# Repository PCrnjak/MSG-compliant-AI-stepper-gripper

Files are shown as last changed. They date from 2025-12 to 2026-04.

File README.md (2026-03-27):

> [!CAUTION]
> The gripper is still in BETA release meaning it will have some bugs from hardware to software!
>

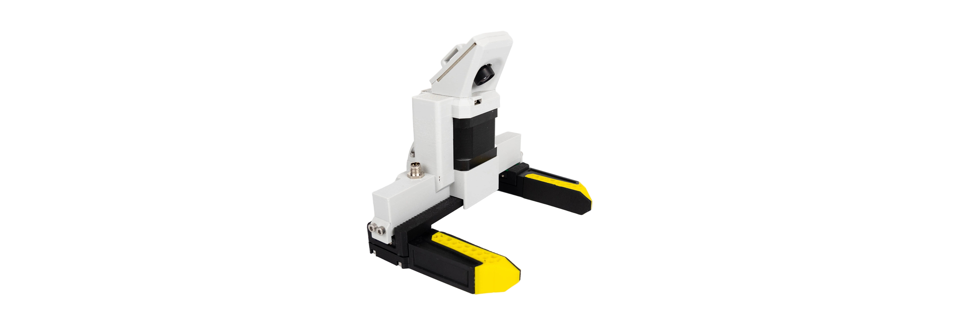
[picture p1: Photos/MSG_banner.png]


<div align="center">

# MSG-compliant-AI-stepper-gripper


     
<p align="center">
  
  
  
  
  
  
</p>

## [▶️YouTube🔴 Video of Gripper in Action!](https://youtu.be/YUvNXfaHM6s)

</div>

## 📖 Project Overview
The **MSG compliant AI stepper gripper** is built around [StepFOC stepper drivers](https://source-robotics.com/products/stepfoc-stepper-controller), which enable precise FOC-based force control on standard stepper motors. This makes it well-suited for assembly tasks, human-robot collaboration, and AI data collection applications — including embodied AI, teleoperation, and VLA training — thanks to its camera-friendly design.

**The gripper is modular in two key ways:**

| Option | Variants | Notes |
|---|---|---|
| Rail length | 100 mm, 150 mm, 200 mm | Determines maximum grip span |
| Stepper length | 21.5 mm, 40 mm, 60 mm | Determines maximum grip force output |

**All mechanical files, firmware, and software are open source, allowing you to attach a custom gripping tool and integrate the gripper with any robotic arm or platform.**

## ⚒️How to build / Where to buy?

You can buy MSG gripper on our website: https://source-robotics.com/products/msg-gripper

If you want to Source all the parts yourself and build your own follow these steps:

Print files from the STEP files folder based on your chosen configuration:

| Rail Size | Folders to Print |
|---|---|
| 100 mm | [Common parts](STEP%20files/Common%20parts) + [Linear rail dependant parts/100mm rail](STEP%20files/Linear%20rail%20dependant%20parts/100mm%20rail) + [Stepper dependant parts/\<your stepper size\>](STEP%20files/Stepper%20dependant%20parts) |
| 150 mm | [Common parts](STEP%20files/Common%20parts) + [Linear rail dependant parts/150mm rail](STEP%20files/Linear%20rail%20dependant%20parts/150mm%20rail) + [Stepper dependant parts/\<your stepper size\>](STEP%20files/Stepper%20dependant%20parts) |
| 200 mm | [Common parts](STEP%20files/Common%20parts) + [Linear rail dependant parts/200mm rail](STEP%20files/Linear%20rail%20dependant%20parts/200mm%20rail) + [Stepper dependant parts/\<your stepper size\>](STEP%20files/Stepper%20dependant%20parts) |

* Source all the parts from the [BOM](https://github.com/PCrnjak/MSG-compliant-AI-stepper-gripper/blob/main/BOM.md)
* Follow [Assembly instructions ](https://youtu.be/EosuDy-heqM) or [Video instructions](https://youtu.be/EosuDy-heqM) to assemble your gripper
* Follow [DOCS](https://source-robotics.github.io/MSG-gripper-docs/) to get your gripper up and running.

## 📚Documentation:

| Resource | Description |
|---|---|
| [Official website](https://source-robotics.com) | Buy the MSG gripper or explore other Source Robotics products |
| [DOCS](https://source-robotics.github.io/MSG-gripper-docs/) | Getting started, wiring, configuration, and full API reference |
| [Python API](https://github.com/PCrnjak/Spectral-BLDC-Python/tree/main) | Control the gripper from Python over CAN bus |
| [BOM](https://github.com/PCrnjak/MSG-compliant-AI-stepper-gripper/blob/main/BOM.md) | Complete list of parts needed to build the gripper |
| [Building instructions *(coming soon)*](https://github.com/PCrnjak/MSG-compliant-AI-stepper-gripper/tree/main/Building%20instructions) | Mechanical assembly walkthrough |
| [URDF & MJCF files](/MSG_gripper_description/) | Ready-to-use robot description files for ROS2, Gazebo, and MuJoCo |
| [ROS2 package — MSG gripper](https://github.com/BiomechatronicsLab/source_robotics_msg_gripper_ros2) | ROS2 driver and example nodes for the MSG gripper |
| [ROS2 package — SSG48 gripper](https://github.com/Lass6230/ssg48_adaptive_electric_gripper_ros2) | ROS2 driver and example nodes for the SSG48 gripper (Should work with MSG also) |

## 💻Quick start code example

```python
import Spectral_BLDC as Spectral
import time

Communication1 = Spectral.CanCommunication(bustype='slcan', channel='COM20', bitrate=1000000)
Motor1 = Spectral.SpectralCAN(node_id=0, communication=Communication1)

Motor1.Send_Clear_Error()
Motor1.Send_gripper_calibrate()
time.sleep(4)

temp_var = 0
while True:
   if temp_var == 0:
      Motor1.Send_gripper_data_pack(50,100,700,1,1,0,0) 
      temp_var = 1
   elif temp_var == 1:
      Motor1.Send_gripper_data_pack(240,100,700,1,1,0,0) 
      temp_var = 0

   message, UnpackedMessageID = Communication1.receive_can_messages(timeout=0.2) 

   if message is not None:
      print(f"Message is: {message}")
      print(f"Node ID is : {UnpackedMessageID.node_id}")
      print(f"Message ID is: {UnpackedMessageID.command_id}")
      print(f"Error bit is: {UnpackedMessageID.error_bit}")
      print(f"Timestamp is: {message.timestamp}")

   time.sleep(3)
```

## 🌐 More about MSG gripper

| YouTube | Instagram | Twitter | LinkedIn |
|---|---|---|---|
|  |  |  |  |

| Discord | Forum | Hackaday | Blog |
|---|---|---| ---|
|  |  |  |  

## ⚠️ Safety, Liability & Disclaimer
This project includes experimental software, hardware designs, and assembly documentation that are still under development and may contain bugs, errors, or incomplete features. By using, building, or modifying this project, you acknowledge that:

* You use this project entirely at your own risk
* You are solely responsible for safe assembly, testing, and operation
* No guarantee is made regarding correctness, safety, or reliability
* The authors are not responsible for any damage, injury, or loss resulting from the use or misuse of this project
* Hardware performance and safety depend on user assembly, component quality, calibration, and handling, which cannot be guaranteed
* This project is provided “as is.” If you choose to build a device yourself using these files, designs, or instructions, you do so without any warranties or guarantees, including regarding safety, reliability, or suitability for any particular purpose.

THIS PROJECT INVOLVES LETHAL VOLTAGES AND OTHER SERIOUS HAZARDS THAT CAN CAUSE SEVERE INJURY. YOU MUST READ THE FULL [SAFETY WARNING AND DISCLAIMER DOCUMENT](SAFETY_WARNING_AND_DISCLAIMER.md)  BEFORE USING ANY PROJECT FILES. BY PROCEEDING, YOU ACKNOWLEDGE AND ACCEPT ALL RISKS AND AGREE TO USE THIS PROJECT ENTIRELY AT YOUR OWN RESPONSIBILITY.

## 💸Support us

The majority of this project is open source and freely available to everyone. Your assistance, whether through donations or advice, is highly valued. Thank you!

 


## 🛡️ Licensing
 Project is under [CERN Open Hardware Licence Version 2 - Strongly Reciprocal](https://github.com/PCrnjak/MSG-compliant-AI-stepper-gripper?tab=CERN-OHL-S-2.0-1-ov-file)

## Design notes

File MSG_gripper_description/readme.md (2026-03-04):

# Source Robotics MSG gripper Description (MJCF) & URDF

> [!IMPORTANT]
> Requires MuJoCo 3.1.3 or later.

## Changelog

See [CHANGELOG.md](./CHANGELOG.md) for a full history of changes.

## Overview

This package contains a simplified robot description (MJCF) and URDF files of the [MSG gripper](https://source-robotics.com/products/msg-gripper) developed by [Source Robotics](https://source-robotics.com/).

There are 2 available MJCF files.

## Online mujoco viewer

https://mujoco-viewer.org/

## URDF folder

[URDF](./URDF/) folder contains:
* MSG gripper

More about URDF here: [Link](./urdf.md)

## URDF → MJCF derivation steps

1. Loaded the URDF into MuJoCo and saved a corresponding MJCF.
2. Manually edited the MJCF to extract common properties into the `<default>` section.
3. Added position-controlled actuators for the arm.
4. Added `scene.xml` which includes the robot, with a textured groundplane, skybox, and haze.

## License

This model is released under an [Apache-2.0 License](LICENSE).

## References

Mjcf reference Mujoco managerie
- references: 
- https://mujoco.readthedocs.io/en/stable/XMLreference.html
- https://github.com/google-deepmind/mujoco_menagerie/tree/main/ufactory_lite6
- https://github.com/google-deepmind/mujoco_menagerie/blob/main/trossen_vx300s/vx300s.xml 
- https://github.com/google-deepmind/mujoco_menagerie/blob/main/aloha/aloha.xml
- https://github.com/google-deepmind/mujoco_menagerie/blob/main/franka_emika_panda/panda.xml 
- https://github.com/jeongeun980906/lerobot-mujoco-tutorial/blob/master/asset/robotis_omy/omy.xml

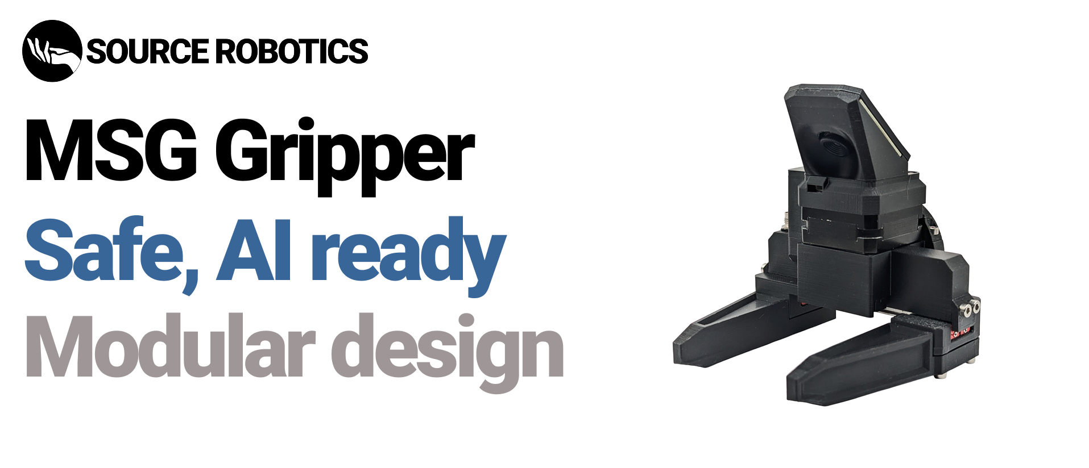
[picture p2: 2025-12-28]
Photos/MSG gripper.png

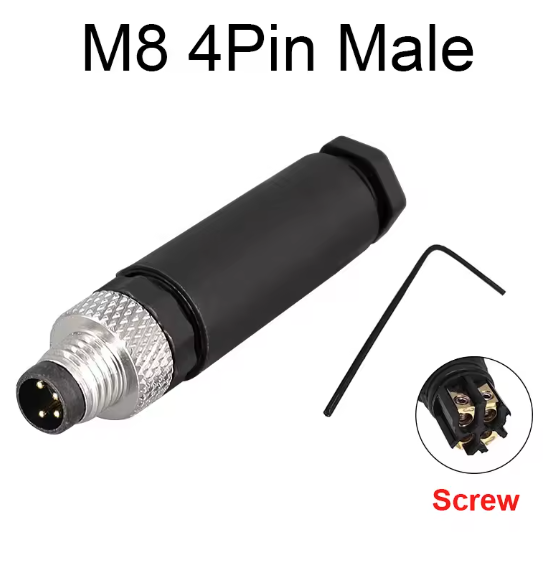
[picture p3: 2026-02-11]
Photos/M8 male.png

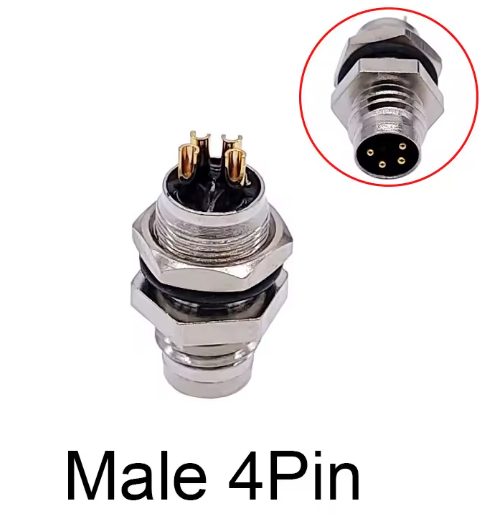
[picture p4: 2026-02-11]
Photos/M8connectormale4pin.png

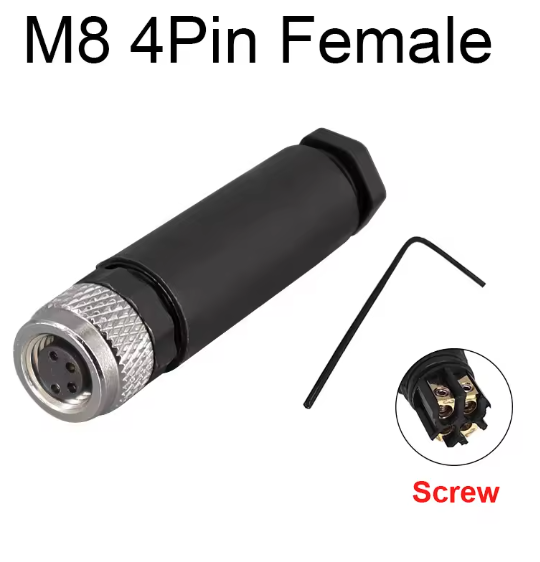
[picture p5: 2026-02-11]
Photos/M8_female.png

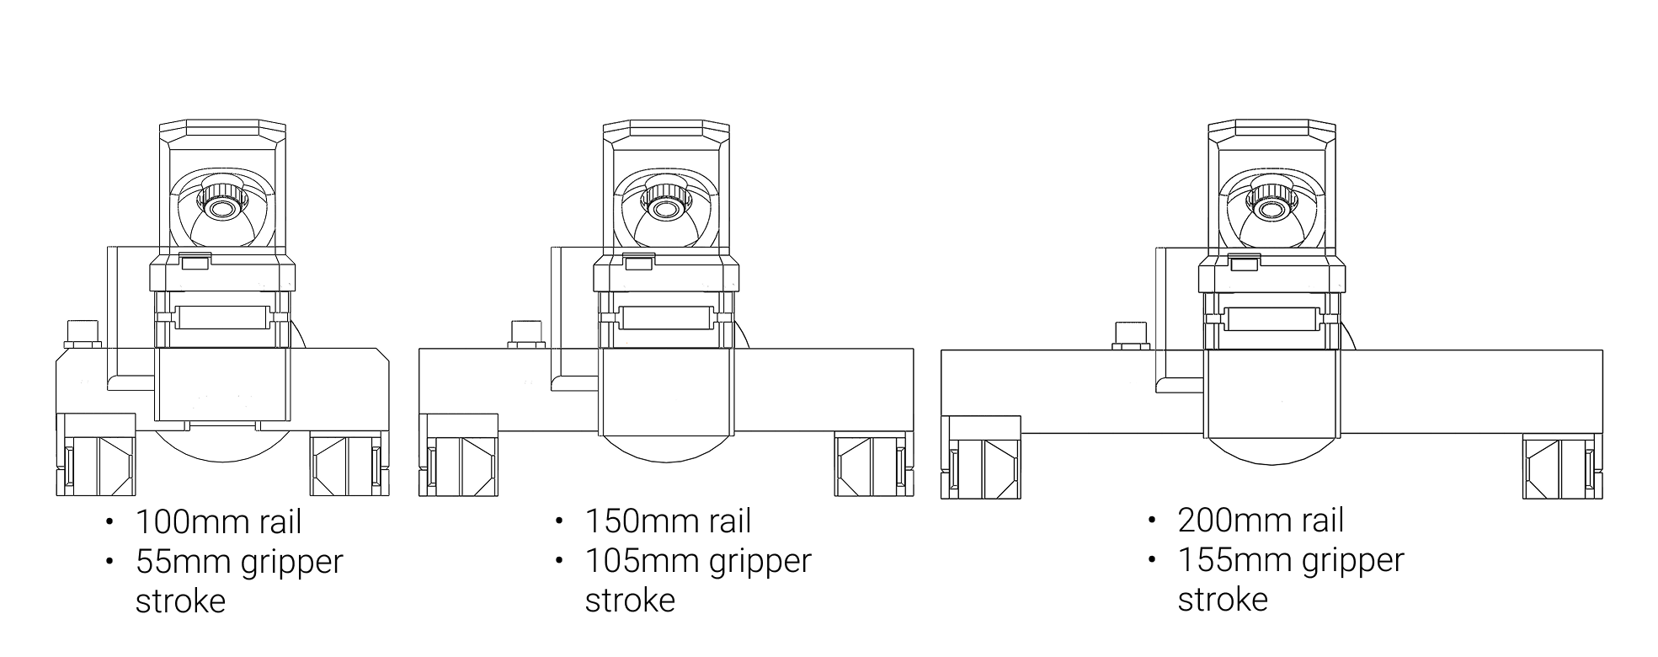
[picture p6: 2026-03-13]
Photos/Gripper_strokes.png

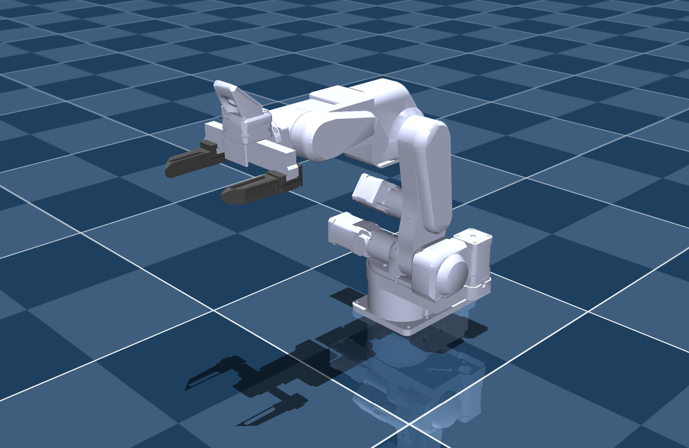
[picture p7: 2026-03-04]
MSG_gripper_description/PAR6_MSG_image.png

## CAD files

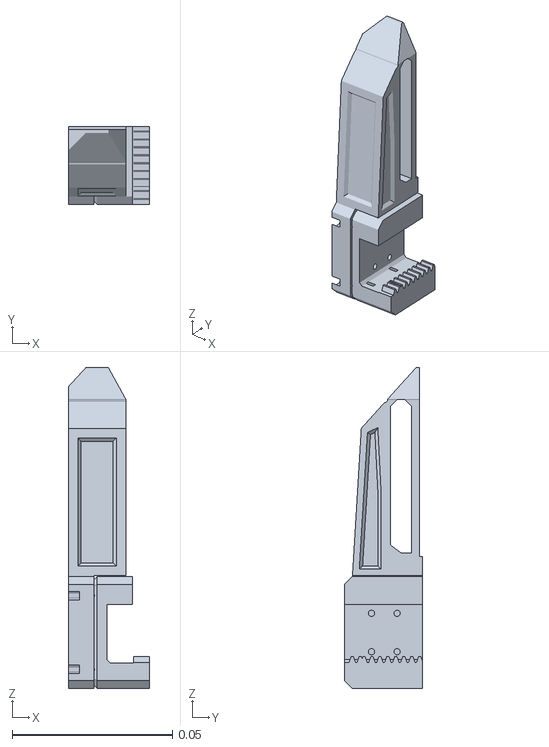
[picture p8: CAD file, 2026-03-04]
MSG_gripper_description/assets/jaw1_MSG.STL
0.0254 x 0.0244 x 0.1

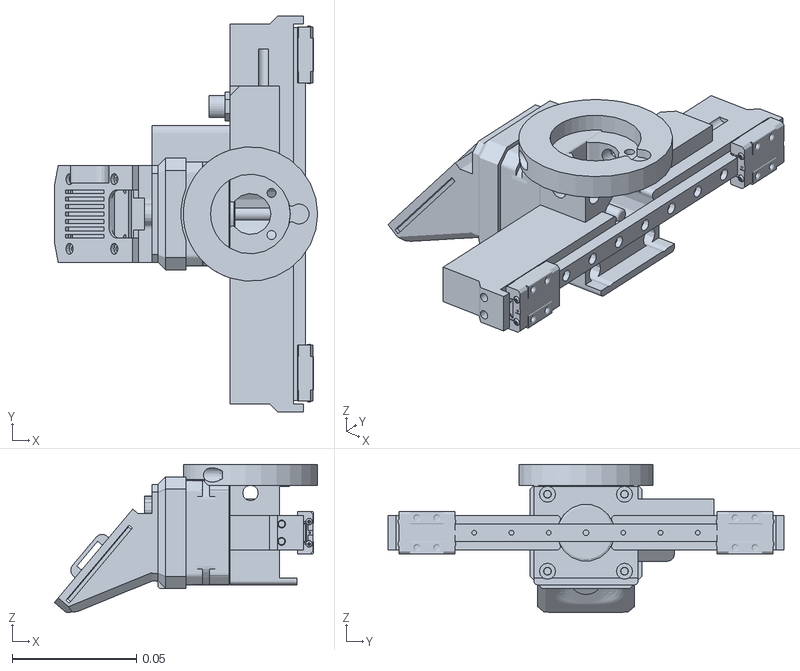
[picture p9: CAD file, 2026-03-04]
MSG_gripper_description/URDF/msg_gripper/meshes/gripper.STL
0.106 x 0.159 x 0.0597

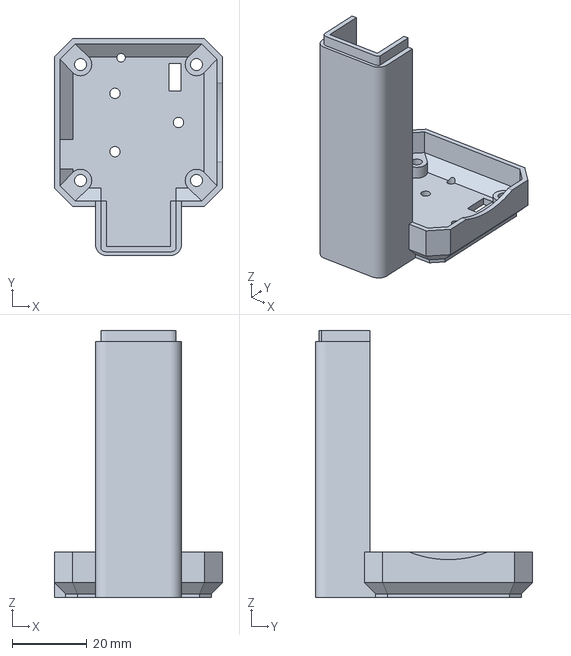
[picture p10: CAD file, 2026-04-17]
Print files/Stepper_cover_60mm.3mf
45.0 x 58.1 x 71.4 mm

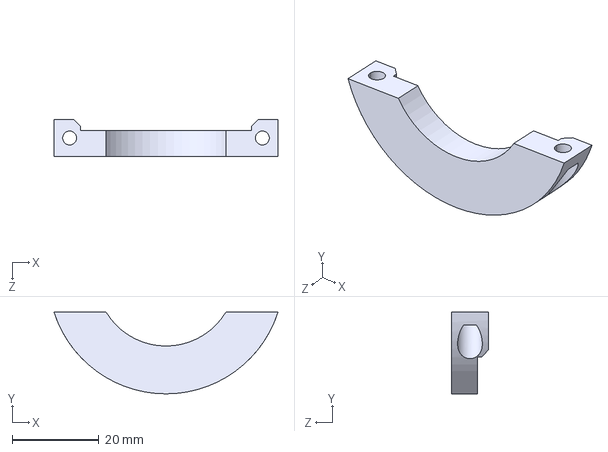
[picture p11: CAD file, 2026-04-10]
STEP files/Common parts/ring_cover.STEP
51.5 x 18.8 x 8.50 mm

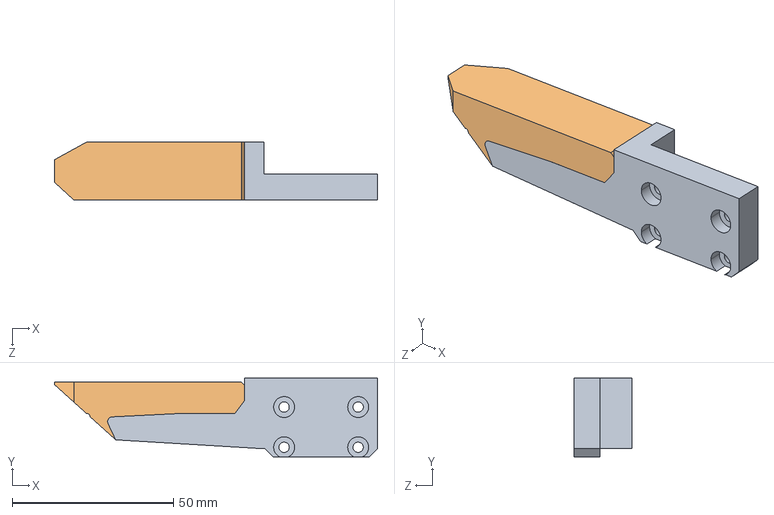
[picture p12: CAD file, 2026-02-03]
STEP files/Gripper jaws attachment/MSG_JAW_TPU_GLUE.STEP
100.3 x 24.4 x 18.0 mm

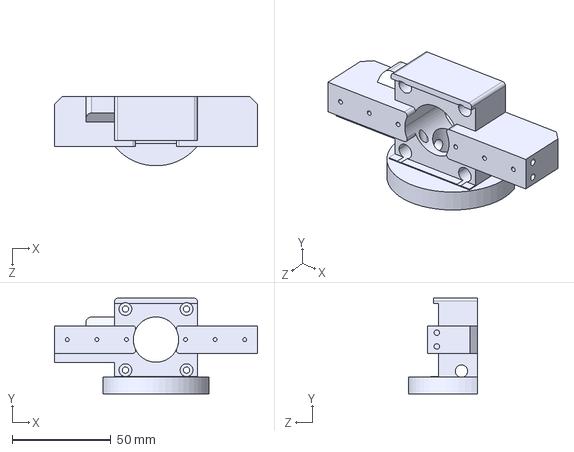
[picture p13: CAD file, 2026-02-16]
STEP files/Linear rail dependant parts/100mm rail/MSG_Gripper_body_100mm.STEP
103.0 x 48.5 x 35.3 mm

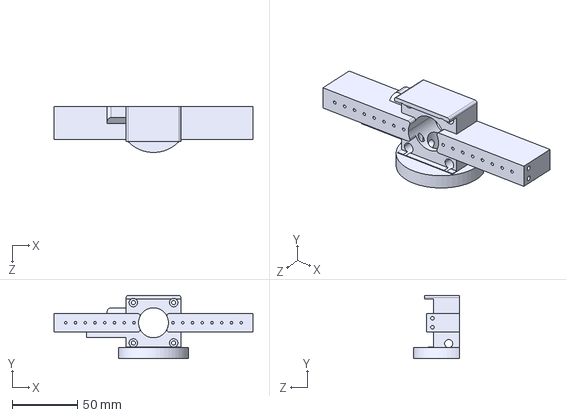
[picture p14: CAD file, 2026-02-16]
STEP files/Linear rail dependant parts/150mm rail/MSG_Gripper_body_150mm.STEP
153.0 x 48.5 x 35.3 mm

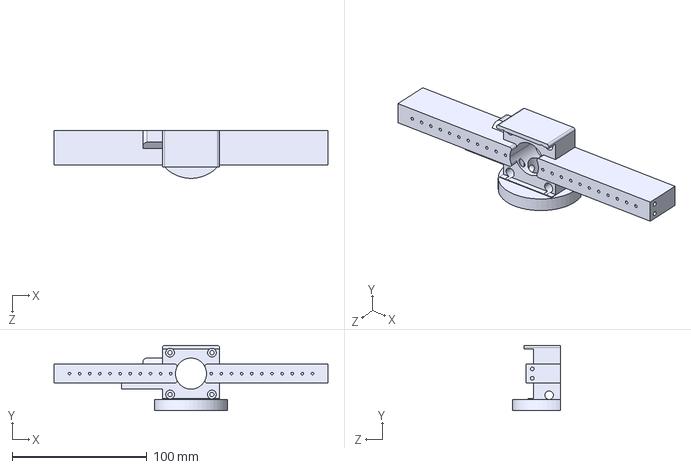
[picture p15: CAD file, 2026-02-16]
STEP files/Linear rail dependant parts/200mm rail/MSG_Gripper_body_200mm.STEP
203.0 x 48.5 x 35.3 mm

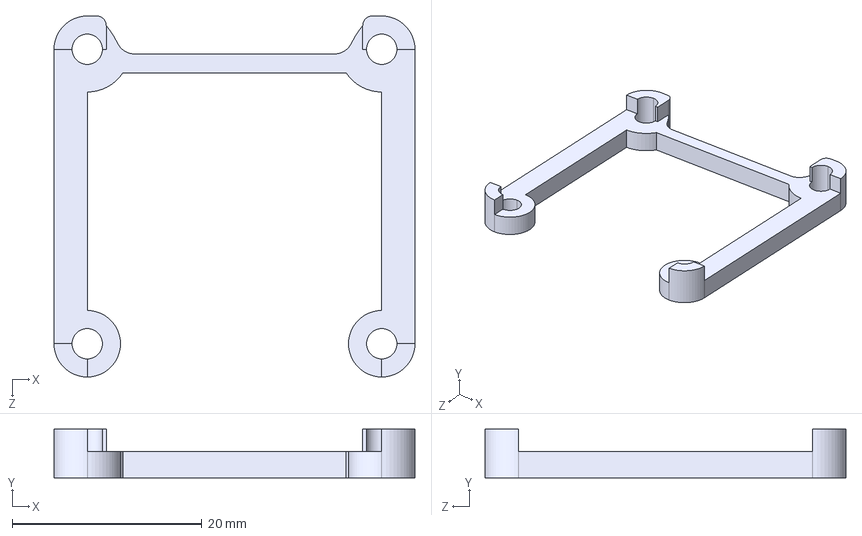
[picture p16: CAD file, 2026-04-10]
STEP files/Stepper dependant parts/21_5mm stepper/Stepper_spacer_J6.STEP
38.0 x 5.15 x 38.0 mm

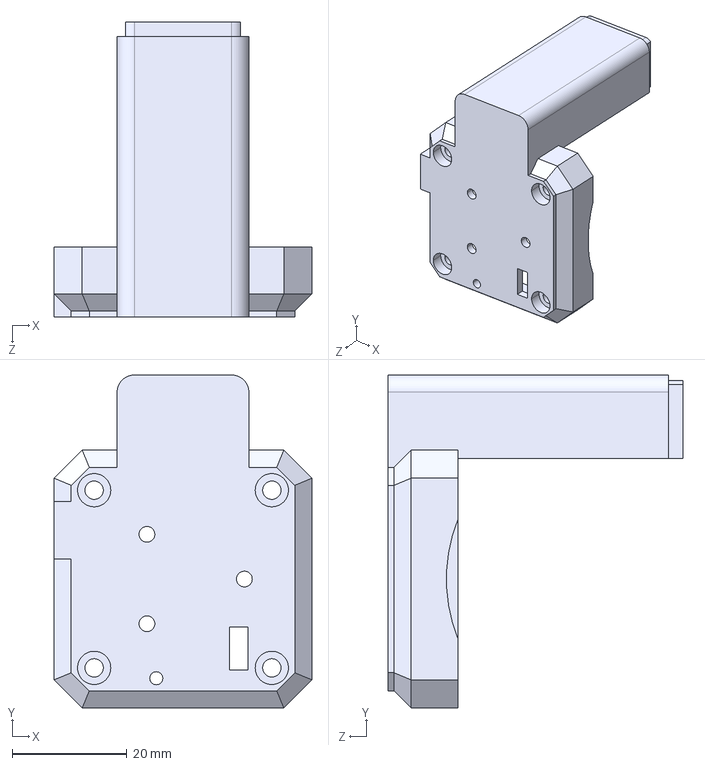
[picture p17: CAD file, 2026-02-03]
STEP files/Stepper dependant parts/40mm stepper/Stepper_cover_40mm.STEP
45.0 x 58.1 x 51.4 mm

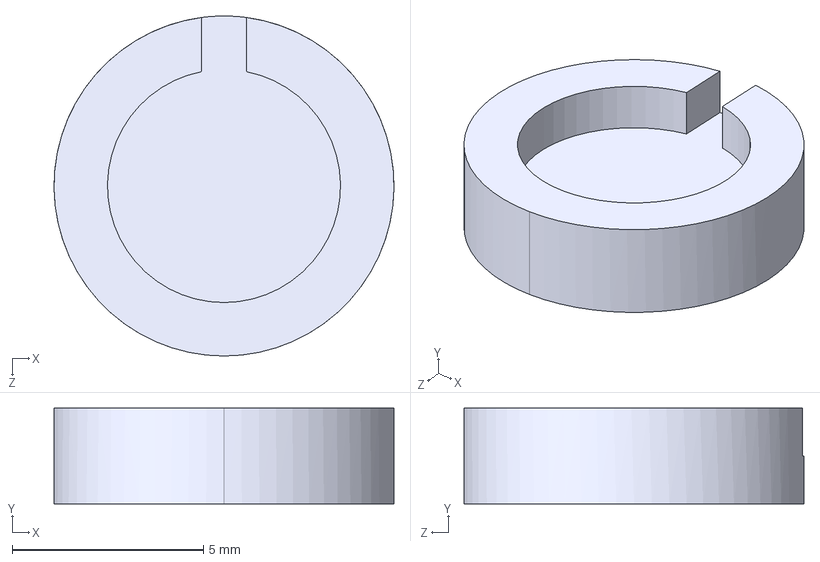
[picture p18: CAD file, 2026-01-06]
STEP files/Stepper dependant parts/Magnet spacers/Magnet_spacer_2.STEP
8.90 x 2.50 x 8.90 mm

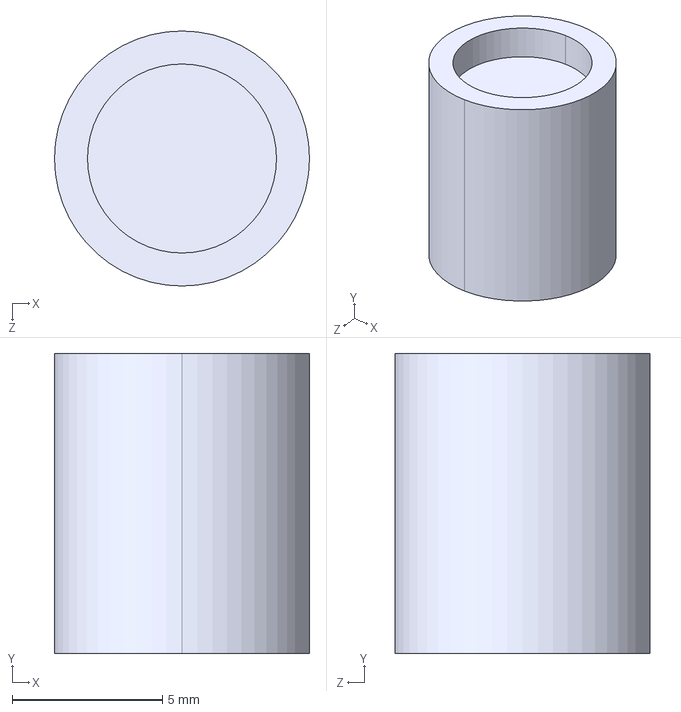
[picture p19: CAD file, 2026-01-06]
STEP files/Tools/Magnet_stepper_tool.STEP
8.50 x 10.0 x 8.50 mm

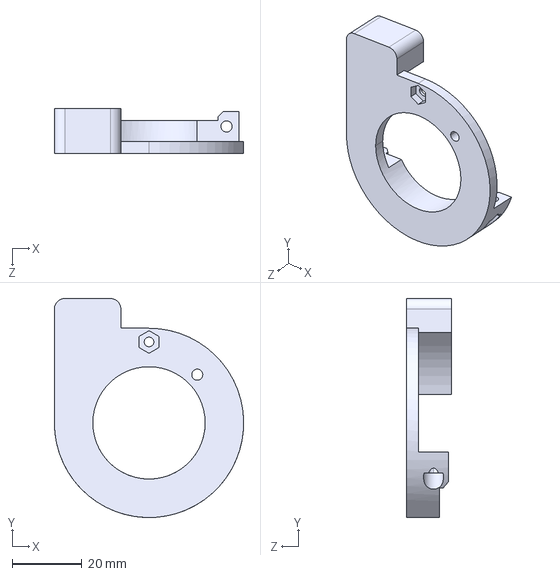
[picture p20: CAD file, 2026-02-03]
STEP files/Common parts/ring_cover-PAROL6.STEP
54.1 x 62.6 x 12.9 mm

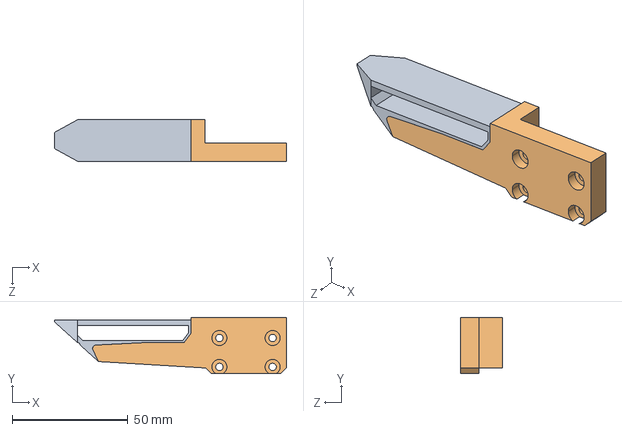
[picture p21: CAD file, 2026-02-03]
STEP files/Gripper jaws attachment/MSG_JAW_2_part.STEP
100.3 x 24.4 x 18.0 mm

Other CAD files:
STEP files/Stepper dependant parts/60mm stepper/Stepper_cover_60mm.STEP
MSG_gripper_description/assets/gripper_MSG.STL
MSG_gripper_description/URDF/msg_gripper/meshes/jaw2.STL
Print files/Stepper_cover_40mm.3mf
MSG_gripper_description/assets/jaw2_MSG.STL
Print files/Common_parts_MSG_gripper.3mf
Print files/MSG_Gripper_body_100mm.3mf
Print files/MSG_Gripper_body_150mm.3mf
Print files/MSG_Gripper_body_200mm.3mf
Print files/Stepper_cover_21_5mm.3mf
Print files/gripper_jaws_100mm.3mf
Print files/gripper_jaws_150mm.3mf
Print files/gripper_jaws_200mm.3mf
STEP files/Common parts/Stepper_spacer_NEMA17.STEP
STEP files/Common parts/camera extension.STEP
STEP files/Common parts/camera_lid.STEP
STEP files/Common parts/connector_lid.STEP
STEP files/Common parts/jaw_blocker.STEP
STEP files/Gripper jaws attachment/MSG_JAW_2_part.3MF
STEP files/Gripper jaws attachment/MSG_JAW_TPU_GLUE.3MF
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

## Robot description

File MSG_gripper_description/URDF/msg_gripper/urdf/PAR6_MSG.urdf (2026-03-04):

<?xml version="1.0" encoding="utf-8"?>
<!-- MSG Gripper only  PAR6 robot arm links removed -->
<robot name="msg_gripper">
  <link name="gripper">
    <inertial>
      <origin xyz="-0.00642470048892474 0.000282668798476438 -0.0695192335056825" rpy="0 0 0" />
      <mass value="0.167623200457379" />
      <inertia ixx="0.000140871735417615" ixy="-9.82778432876683E-07" ixz="-2.72691487145471E-06" iyy="2.45392416247037E-05" iyz="-2.78909378823719E-07" izz="0.00013036472950858" />
    </inertial>
    <visual>
      <origin xyz="0 0 0" rpy="0 0 0" />
      <geometry>
        <mesh filename="package://msg_gripper/meshes/gripper.STL" />
      </geometry>
      <material name="">
        <color rgba="0.792156862745098 0.819607843137255 0.933333333333333 1" />
      </material>
    </visual>
    <collision>
      <origin xyz="0 0 0" rpy="0 0 0" />
      <geometry>
        <mesh filename="package://msg_gripper/meshes/gripper.STL" />
      </geometry>
    </collision>
  </link>
  <link name="jaw1">
    <inertial>
      <origin xyz="0.000317390129572659 -0.0636011550113124 -0.0505219142777576" rpy="0 0 0" />
      <mass value="0.0267240448883812" />
      <inertia ixx="1.05776518737304E-05" ixy="4.17466317108795E-08" ixz="-4.94412707881078E-07" iyy="1.02820791329259E-05" iyz="5.30501392593403E-07" izz="1.56447936575552E-06" />
    </inertial>
    <visual>
      <origin xyz="0 0 0" rpy="0 0 0" />
      <geometry>
        <mesh filename="package://msg_gripper/meshes/jaw1.STL" />
      </geometry>
      <material name="">
        <color rgba="0.29804 0.29804 0.29804 1" />
      </material>
    </visual>
    <collision>
      <origin xyz="0 0 0" rpy="0 0 0" />
      <geometry>
        <mesh filename="package://msg_gripper/meshes/jaw1.STL" />
      </geometry>
    </collision>
  </link>
  <joint name="joint_jaw1" type="prismatic">
    <origin xyz="0.02835 0 -0.1409" rpy="-3.1416 0 3.1416" />
    <parent link="gripper" />
    <child link="jaw1" />
    <axis xyz="0 -1 0" />
    <limit lower="-0.052" upper="0" effort="20" velocity="0.1" />
  </joint>
  <link name="jaw2">
    <inertial>
      <origin xyz="0.000313277058697659 0.0636017321420815 -0.0494862901594326" rpy="0 0 0" />
      <mass value="0.0267245850480152" />
      <inertia ixx="1.05767573086608E-05" ixy="-4.18351972636844E-08" ixz="-7.32706121136976E-07" iyy="1.02816308296904E-05" iyz="-5.3239570329707E-07" izz="1.56361148863754E-06" />
    </inertial>
    <visual>
      <origin xyz="0 0 0" rpy="0 0 0" />
      <geometry>
        <mesh filename="package://msg_gripper/meshes/jaw2.STL" />
      </geometry>
      <material name="">
        <color rgba="0.29804 0.29804 0.29804 1" />
      </material>
    </visual>
    <collision>
      <origin xyz="0 0 0" rpy="0 0 0" />
      <geometry>
        <mesh filename="package://msg_gripper/meshes/jaw2.STL" />
      </geometry>
    </collision>
  </link>
  <joint name="joint_jaw2" type="prismatic">
    <mimic joint="joint_jaw1" multiplier="-1" offset="0"/>
    <origin xyz="0.02835 0 -0.1409" rpy="-3.1416 0 3.1416" />
    <parent link="gripper" />
    <child link="jaw2" />
    <axis xyz="0 -1 0" />
    <limit lower="0" upper="0.052" effort="20" velocity="0.1" />
  </joint>

  <transmission name="jaw_transmission">
    <type>transmission_interface/SimpleTransmission</type>
    <joint name="joint_jaw1">
      <hardwareInterface>PositionJointInterface</hardwareInterface>
    </joint>
    <actuator name="jaw_motor">
      <hardwareInterface>PositionJointInterface</hardwareInterface>
      <mechanicalReduction>1</mechanicalReduction>
    </actuator>
  </transmission>

</robot>

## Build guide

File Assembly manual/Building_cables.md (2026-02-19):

## MSG & SSG48 gripper cable

Buy Official cables from Source Robotics: [Link](https://source-robotics.com/)

Parts needed if DIY your own cable:

| Type | Length / Spec | Quantity | Description | Link |
|---|---|---|---|---|
| 26 AWG cable | 0.15 mm², 4-wire twisted pair | 0.4 m | ~40 cm usually sufficient | [Link](https://s.click.aliexpress.com/e/_c4m3ggwn) |
| M8 4-pin male wire connector | — | 1 | [See reference image](../Photos/M8%20male.png) |[Link](https://s.click.aliexpress.com/e/_c4OWHPKF) |
| M8 4-pin female wire connector | — | 1 | [See reference image](../Photos/M8_female.png) | [Link](https://s.click.aliexpress.com/e/_c4OWHPKF) |

> [!NOTE]
>     **PAROL6 and PAR6 use different cables for SSG48 and MSG grippers. Using incorrect one can damage your robot**

## Wire diagram for PAROL6 robotic arm

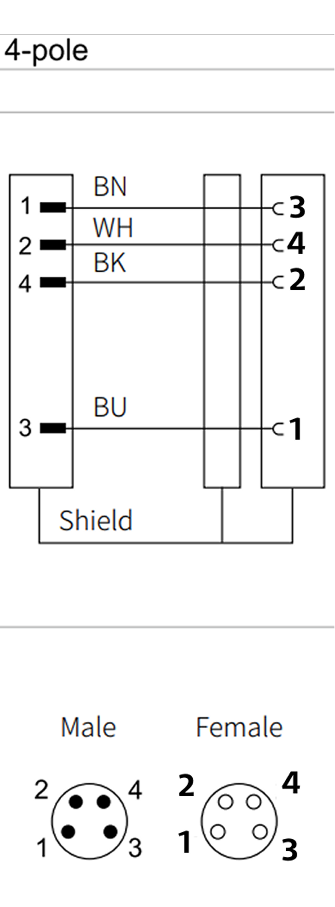
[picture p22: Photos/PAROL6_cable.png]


## Wire diagram for PAR6 robotic arm
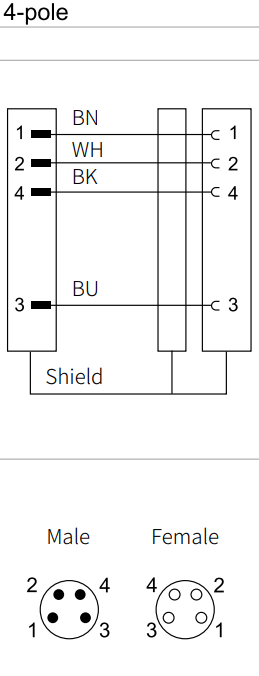
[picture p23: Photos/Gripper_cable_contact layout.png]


## Final look of the cable 

End result of this cable assembly needs to look like this:

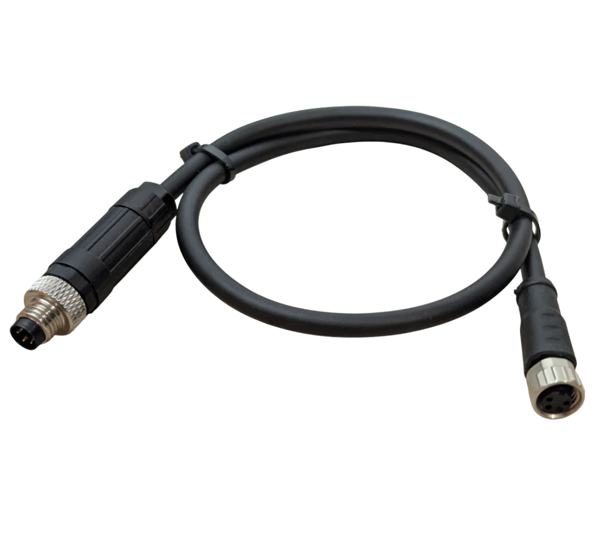
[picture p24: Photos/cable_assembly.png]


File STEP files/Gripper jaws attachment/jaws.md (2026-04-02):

FOR TPU JAWS USE 16% INFILL FOR OPTIMAL SOFTNESS WITH NO TOP AND BOTTOM LAYERS!

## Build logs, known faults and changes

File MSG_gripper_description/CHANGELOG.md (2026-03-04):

# Changelog – Source Robotics PAR6 Description

All notable changes to this model will be documented in this file.

## [10-2-2025]
- Added the initial files:
    - MJCF for PAR6 with SSG48 and MSG grippers
    - URDF files for 3 versions: PAR6 with flange, SSG48 gripper and MSG gripper
    - Added extra jaw options for SSG48 gripper

## [4-3-2025]
- From the initial release of PAR6 files we extracted:
    - URDF models of MSG and SSG48 gripper
    - MJCF models of MSG and SSG48 gripper

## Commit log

2025-12-07 Update README with caution about experimental branch
    Added caution note about experimental kinematics branch usage and its risks.
2025-12-28 Initial steps
    [MSG_Gripper_body_100mm.STEP, MSG_Gripper_body_150mm.STEP, Stepper_cover_21_5mm.STEP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]
2025-12-28 Revise README for MSG-compliant AI stepper gripper
    Updated README to reflect new gripper information and removed outdated content.
2026-01-06 added steps
    [MSG_Gripper_body_200mm.STEP, MSG_solid_jaw.STEP, Magnet_spacer.STEP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]
2026-01-06 initial BOM
2026-01-07 update BOM
2026-02-03 jaws update
    [MSG_JAW_2_part.3MF, MSG_JAW_2_part.STEP, MSG_JAW_TPU_GLUE.3MF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]
2026-02-11 Update to BOM
2026-02-16 Updated STEPS for real M8 nuts
    [MSG_Gripper_body_100mm.STEP, MSG_Gripper_body_150mm.STEP, MSG_Gripper_body_200mm.STEP]
2026-02-19 Added cable assembly manual
2026-03-04 Added URDF and MJCF files
    [PAR6_MSG.csv, PAR6_MSG.urdf, gripper.STL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]
2026-03-13 Remove image reference for gripper strokes
    Removed image reference for gripper strokes from README.
2026-03-27 Update video link for assembly instructions
2026-04-02 updated jaws
    [Common_parts_MSG_gripper.3mf, gripper_jaws_100mm.3mf, gripper_jaws_150mm.3mf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]
2026-04-04 Add more STL files
    [MSG_Gripper_body_100mm.3mf, MSG_Gripper_body_150mm.3mf, MSG_Gripper_body_200mm.3mf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]
2026-04-10 update steps
    [Stepper_spacer_J6.STEP]
2026-04-10 update ring cover
    [ring_cover.STEP]
2026-04-17 update 60mm stepper body
    [Stepper_cover_60mm.3mf, Stepper_cover_60mm.STEP]

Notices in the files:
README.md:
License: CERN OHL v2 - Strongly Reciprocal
